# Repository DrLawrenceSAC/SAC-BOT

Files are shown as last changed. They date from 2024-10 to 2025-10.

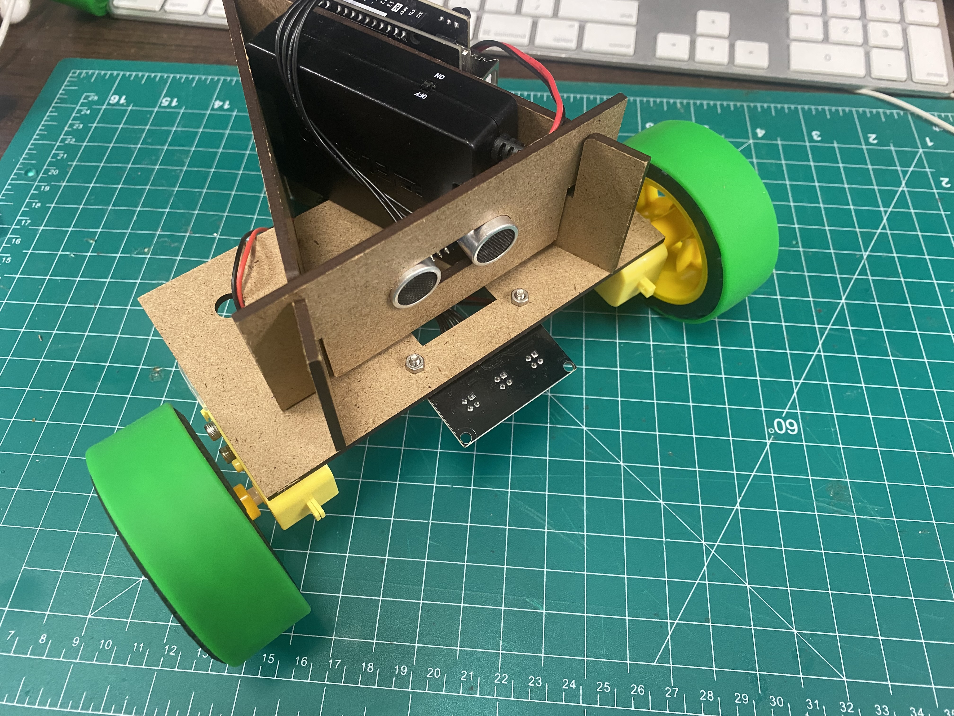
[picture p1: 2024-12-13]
RescueLine/images/IMG_2231.jpg

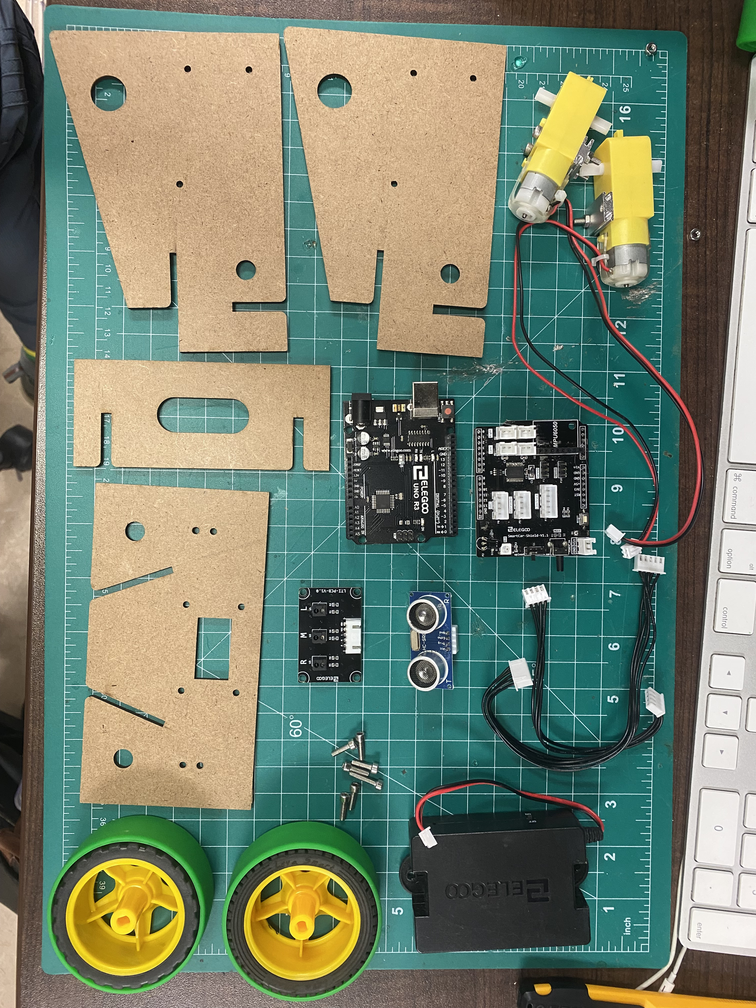
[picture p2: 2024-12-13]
RescueLine/images/IMG_2234.jpg

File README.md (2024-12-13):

# SAC-BOT
A repository for the design and development of low-cost, open-source, beginner robotics platforms tailored to competition in RoboCup Junior events.

The design goals for these designs are as follows:
- low-cost for ease of addoption within and beyond our program
- functional, not perfect - allowing immediate engagement, and encouraing student-led modification and improvement.
- designed for specific goals of [RoboCup Junior](https://www.robocup.org/)

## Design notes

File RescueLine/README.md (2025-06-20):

# Rescue - Line

A project to create a simple, functional, low-cost robot for use in RoboCup Junior Rescue Line competition. [Full competition information and rules can be found here](https://junior.robocup.org/rcj-rescue-line/).

The current design (version 7.4) is created to use as many simple parts that may be available in a given technology classroom (TT motors, arduino boards etc.)

The design files include laser cutting files and fusion 360 design files. The design is created to be cut from 3 mm (1/8 inch) thick MDF wood. It can be modified and improved, made out of cardboard or have components hot-glued on. The design is intentionally functional, but not optimal. This is a choice to encourage student design and modification in the spirit of RoboCup.

A video of the working robot showing line following and obstacle avoidance in a student activity is included in this directory.

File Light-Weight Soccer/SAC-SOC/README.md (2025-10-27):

# SAC-SOC

A minimal robot based on the simple design of the SAC-BOT for soccer robot construction.

## Stage One: Robotic Design Overview

### Plate 1 - Drive System

- **Motors:** Four TT motors positioned at 90° from each other
- **Wheels:** Standard plastic wheels (utilizing slipperiness for omni-drive functionality)
- **Assembly:** Motors bolted into place
- **Wiring:** Four wires run upward to Plate 2

### Plate 2 - Control System

- **Microcontroller:** Arduino Uno
- **Motor Control:** Motor controller mounted
- **Servos:** Two servos mounted for Plate 3 positioning

### Plate 3 - Sensor Array

- **Location:** Positioned above the motor driver
- **Sensors:** IR sensors with cicada pattern angle detection
- **Purpose:** Player ball detection

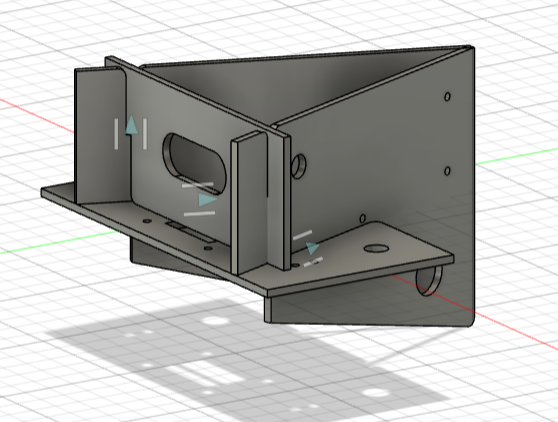
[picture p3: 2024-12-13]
RescueLine/images/2425-RoboCup-SACBOTV6.png

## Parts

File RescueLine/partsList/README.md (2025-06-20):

# Parts List

Below are the parts required for the SAC-BOT rescue line robot. A source link to supplier DigiKey is also included.

List is shared at (digikey.ca here)[https://www.digikey.ca/en/mylists/list/CZCZJ5AE1T].

The above link includes several extra parts (jumper wires, bolts and nuts) that might also be needed.

Not included! -> battery and battery holder we use a two-cell 18650 Lithium batter holder with a case. No sources from digikey, many on amazon and other providers.

| Digi-Key Part Number | Manufacturer | Manufacturer Part Number | Requested Part Number | Description | Customer Reference | Quantity | Unit Price | Extended Price |
| --- | --- | --- | --- | --- | --- | --- | --- | --- |
| 1738-1228-ND | DFRobot | DFR0216 | 1738-1228-ND | DFRDUINO UNO V3.0 ATMEGA328P | 1 | 19.17 | $19.17 | $19.17 |
| 1738-1078-ND | DFRobot | DRI0009 | 1738-1078-ND | 2A MOTOR SHIELD FOR ARDUINO | 1 | 20.66 | $20.66 | $20.66 |
| 1597-114090050-ND | Seeed Technology Co., Ltd | 1.14E+08 | 1597-114090050-ND | STANDARD MOTOR 210 RPM 3-7.2V | 2 | 1.9 | $3.80 | $3.80 |
| 1528-2711-ND | Adafruit Industries LLC | 3942 | 1528-2711-ND | ULTRASONIC SENSOR SONAR DISTANCE | 1 | 6.26 | $6.26 | $6.26 |
| 1568-1556-ND | SparkFun Electronics | SEN-11769 | 1568-1556-ND | SPARKFUN REDBOT SENSOR - LINE FO | 3 | 5.2 | $15.60 | $15.60 |
| 1528-2587-ND | Adafruit Industries LLC | 3763 | 1528-2587-ND | THIN WHITE WHEEL FOR TT DC GEARB | 2 | 2.38 | $4.76 | $4.76 |
| | | | | | | |Total: | $70.25 |

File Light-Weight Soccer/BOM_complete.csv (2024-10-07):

link | name | cost(cad) | amount | purpose
https://www.aliexpress.com/item/1005001456186625.html | WeAct BlackPill STM32F411CEU6 STM32F411 STM32F4 STM32 Core Board Learning Board Development Micropython | $5 | 2 | central processor
https://www.sparkfun.com/products/15335 | SparkFun 9DoF IMU Breakout - ICM-20948 (Qwiic) | $25.50 | 1 | IMU
N/A | IR PCB | $20 (Depending on bulk pricing) | 1 | IR Ball detection
N/A | Colour Sensor PCB | $40 | 1 | line detection
https://www.aliexpress.com/item/1005006213948214.html | JGA25-370 Mini Motor DC 12 Volt 3V 6V 24V High Torque Low Speed Reversed Electric Motor Reduction Engine 12v Gear Motor | $6 | 4 | Motors
N/A | Main PCB | $20 | 1 | Main PCB for mounting hardware
N/A | Misc Hardware/3D prints | $10 | 1 | Misc
https://www.amazon.ca/daier-2-5-4-Connector-200mm-Female/dp/B01DUC1S14 | daier 20 Sets Jst XH 2.54 4 Pin Connector Plug Male with 200mm Wire & Female Connector | $0.50 | 1 | Connector for IR PCB and connector joint
https://www.pololu.com/product/4733 | MP6550 Single Brushed DC Motor Driver Carrier | $6.31 | 4 | Motor Drivers
https://www.amazon.ca/Zeee-1300mAh-Quadcopter-Helicopter-Airplane/dp/B08CDT38CL | Zeee 11.1V 1300mAh Lipo Battery 120C 3S RC Battery with XT60 Plug for FPV Racing Drone Quadcopter Helicopter Airplane RC Boat RC Car RC Models(2 Pack) | $25 | 1 | Battery
https://www.pololu.com/product/2858 | Pololu 5V 2.5A Step-Down Voltage Regulator D24V22F5 | $16.58 | 1 | Regulator - Step Down
https://www.amazon.ca/2-54MM-Female-Single-Connector-Wires/dp/B07YJ2RKYF?s=industrial | 30 Sets JST XH 2.54MM 2 Pin Female Single Connector with Flat Wires 100MM 1007 26AWG | $0.50 | 1 | Motor to Board connector

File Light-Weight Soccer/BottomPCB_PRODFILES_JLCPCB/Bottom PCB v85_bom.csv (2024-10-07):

Comment | Designator | Footprint | LCSC Part #
1k | R1 R10 R11 R12 R13 R14 R15 R16 R17 | 0603
20 | R2 R3 R4 R5 R6 R7 R8 R9 | RESC3224X71
100nF | C1 C2 C3 C4 | WCAP-CSGP_0603_W
ICM-20948_SPARKFUN_I2C | U$2 | ICM-20948_SPARKFUN_I2C
JE2835ARD-N-0001A0000-N0000001 | LED1 LED2 LED3 LED4 LED5 LED6 LED7 LED8 | JE2835ARDN0001A0000N0000001
LED_GREEN | D1 | LEDC1005X25N_FLAT-G
MINISTM32F4X1 | U$1 | MINISTM32F4X1
MP6550_POLOLU | M1 M2 M3 M4 | MP6550_POLOLU
PINHD-1X2 | JP3 JP4 JP5 JP6 | 1X02
PINHD-1X4/90 | JP1 | 1X04/90
PINHD-1X55X2MM | JP2 JP7 JP8 JP9 | 1_05X2MM
SRD-12VDC-SL-C | K1 | RELAY_SRD-12VDC-SL-C
SSSF021500 | S1 S2 | SSSF021500
VBPW34S | D2 D3 D4 D5 D6 D7 D8 D9 | VBPW34S
XT60-M | J1 | AMASS_XT60-M

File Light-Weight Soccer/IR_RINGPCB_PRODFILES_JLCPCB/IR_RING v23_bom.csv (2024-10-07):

Comment | Designator | Footprint | LCSC Part #
MINISTM32F4X1 | U$1 | MINISTM32F4X1
PINHD-1X4 | JP1 | 1X04
PINHD-1X4/90 | JP2 JP3 JP4 JP5 JP6 | 1X04/90
TSSP4038 | IC1 IC2 IC3 IC4 IC5 IC6 IC7 IC8 IC9 IC10 IC11 IC12 | TSSP4038

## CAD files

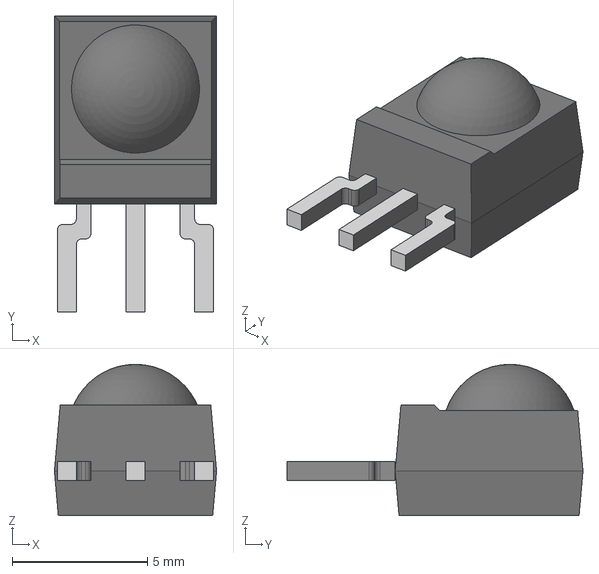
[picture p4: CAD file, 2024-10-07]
Light-Weight Soccer/Design Files/3D Models/TSSP4038_v1.step
6.00 x 10.9 x 5.60 mm

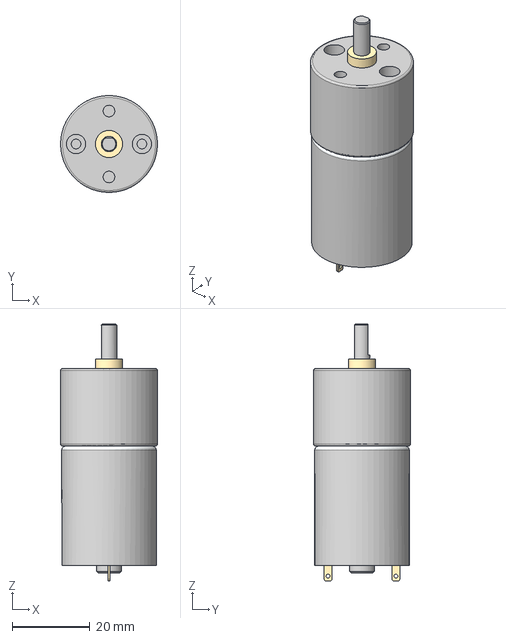
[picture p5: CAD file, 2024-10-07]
Light-Weight Soccer/Design Files/3D Models/dc motor2 v1_v1.step
25.0 x 25.0 x 66.3 mm

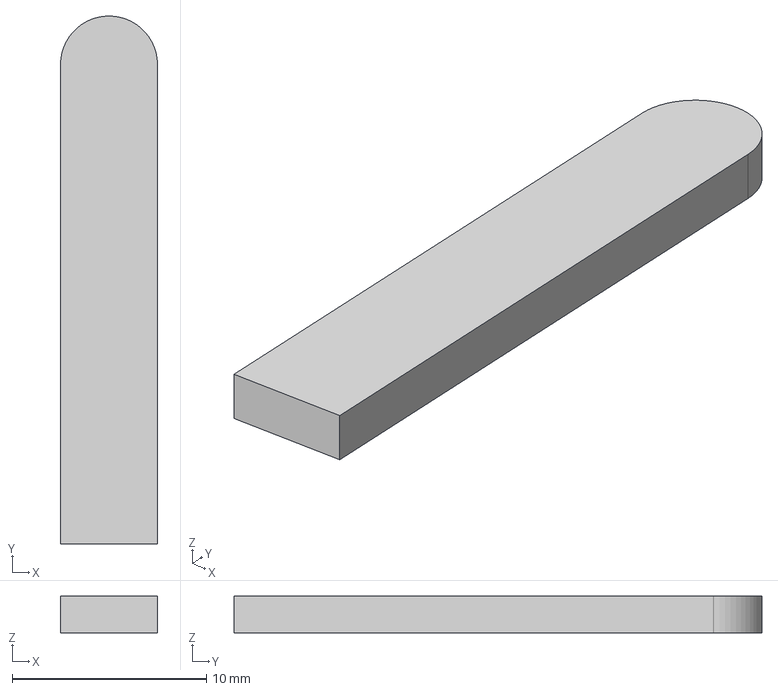
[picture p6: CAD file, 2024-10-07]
Light-Weight Soccer/Design Files/3D Models/Open Funnel_Component2_v1.step
5.00 x 27.2 x 1.90 mm

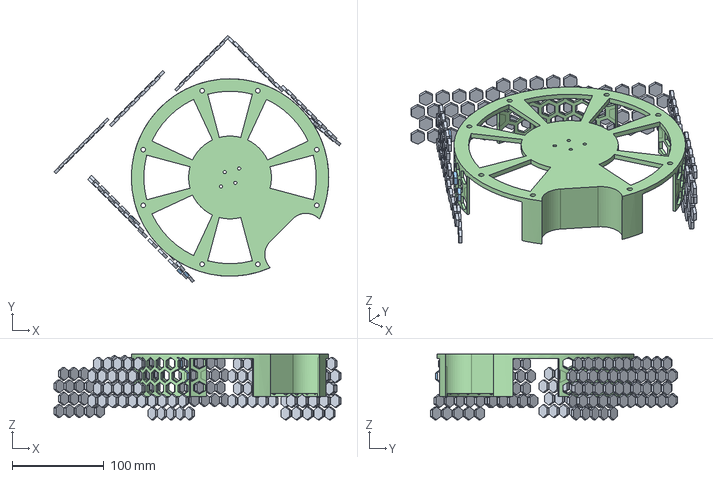
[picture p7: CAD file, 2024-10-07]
Light-Weight Soccer/Design Files/3D Models/Base Cover_v4.step
312.5 x 269.0 x 71.3 mm
honeycomb design x 7
honeycomb design v0(Mirror) x 3

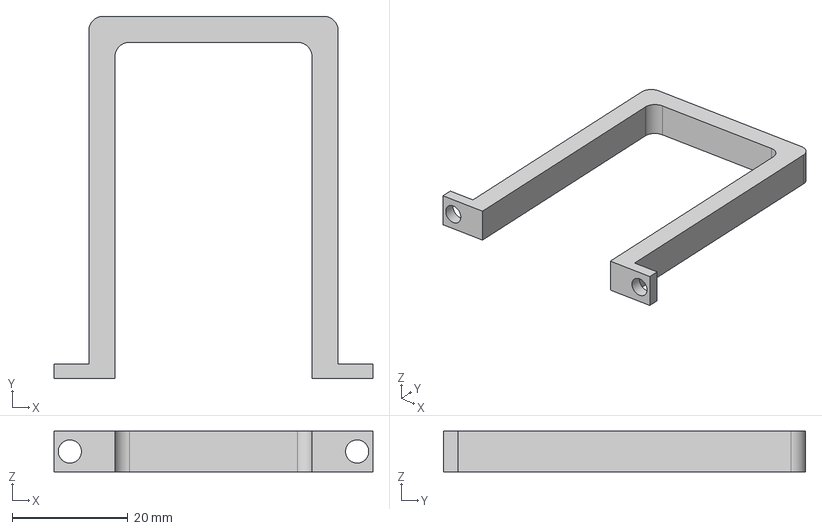
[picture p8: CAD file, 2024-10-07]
Light-Weight Soccer/Design Files/3D Models/Handle_v3.step
55.0 x 62.5 x 7.00 mm

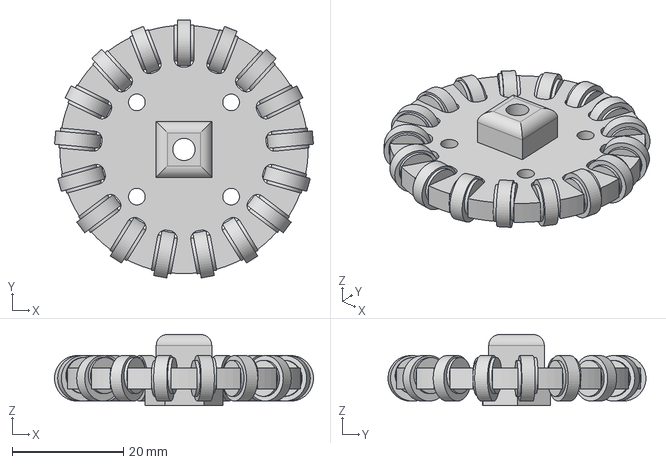
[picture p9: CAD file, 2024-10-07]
Light-Weight Soccer/Design Files/3D Models/gtf_robots_50mm_x_6mm_nGoLKr v4_v1.step
46.6 x 46.4 x 12.8 mm

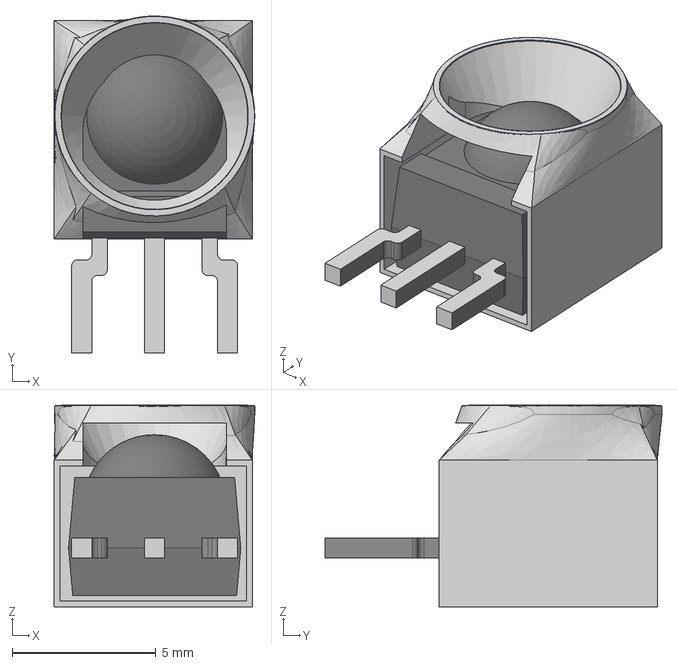
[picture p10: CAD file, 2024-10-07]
Light-Weight Soccer/Design Files/3D Models/Closed Funnel_v1.step
6.99 x 11.7 x 7.03 mm
Open Funnel v1
TSSP4038

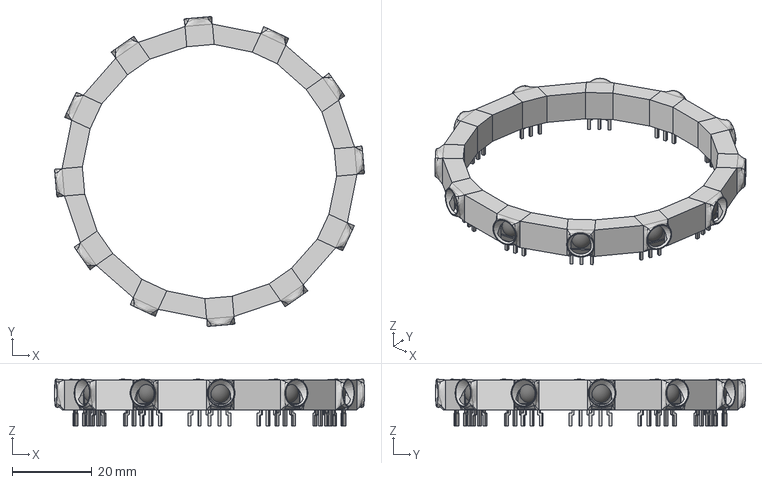
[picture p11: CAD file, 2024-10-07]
Light-Weight Soccer/Design Files/3D Models/IR_RING_MODEL_v2.step
77.8 x 77.8 x 11.7 mm
Open Funnel v1 x 12
TSSP4038 x 12

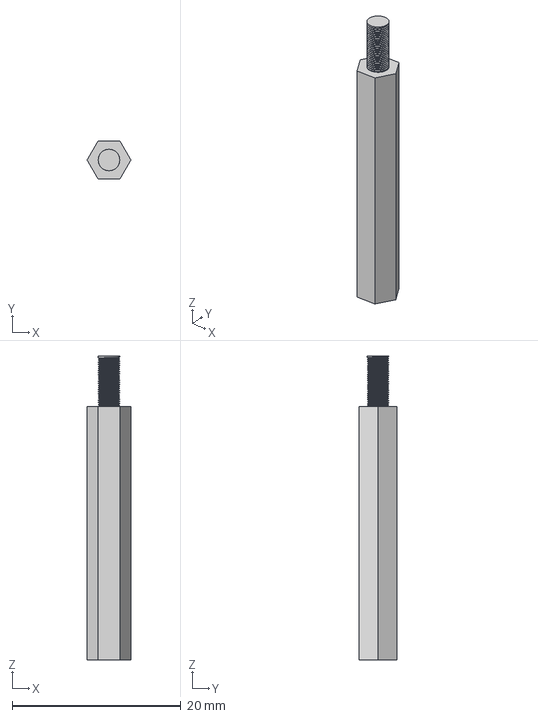
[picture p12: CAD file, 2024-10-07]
Light-Weight Soccer/Design Files/3D Models/stand off v1_v1.step
5.20 x 4.50 x 36.0 mm

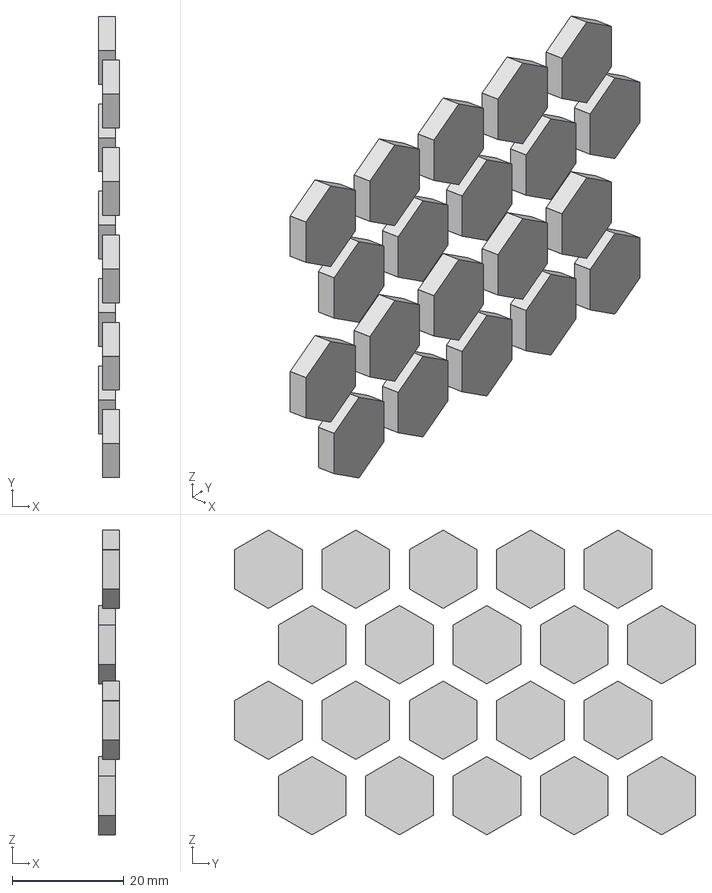
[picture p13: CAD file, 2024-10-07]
Light-Weight Soccer/Design Files/3D Models/honeycomb design_v1.step
3.72 x 82.4 x 54.5 mm

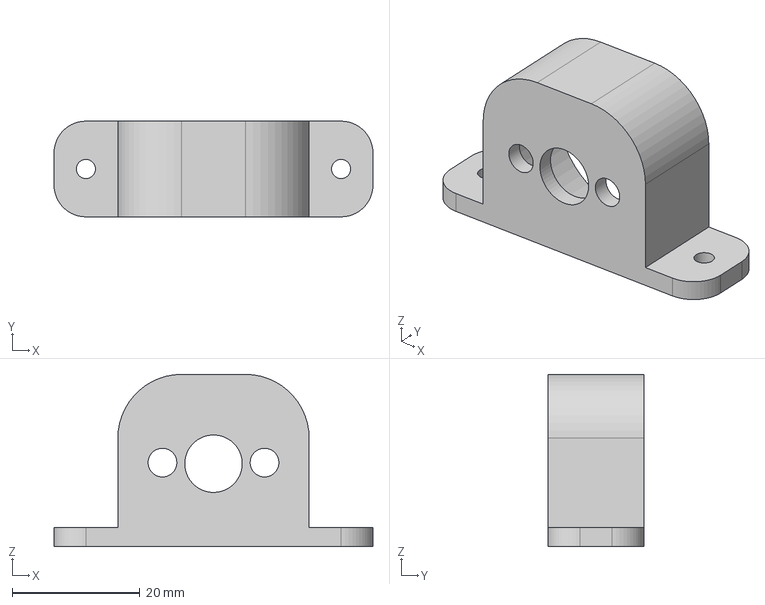
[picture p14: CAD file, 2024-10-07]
Light-Weight Soccer/Design Files/3D Models/motor mount v5_v2.step
50.0 x 15.0 x 27.0 mm

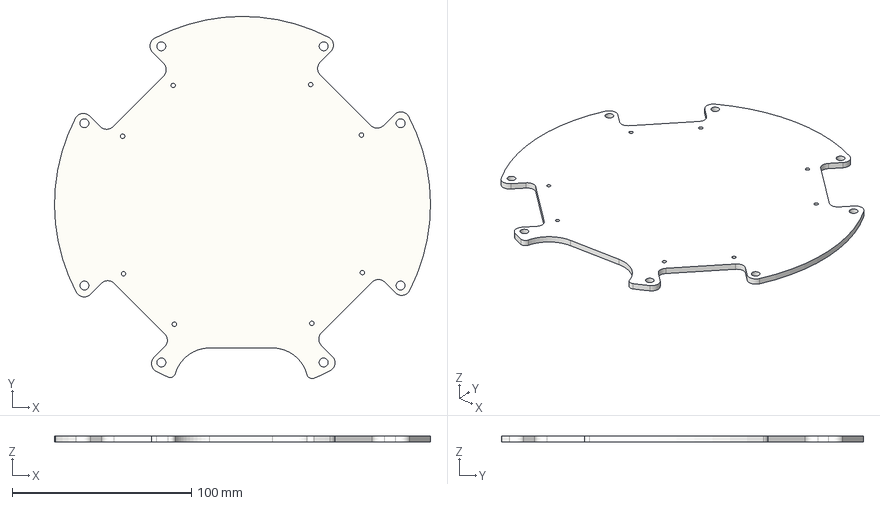
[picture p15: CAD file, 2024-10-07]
Light-Weight Soccer/Design Files/3D Models/Bottom Shape v16_v1.step
210.0 x 202.3 x 3.50 mm

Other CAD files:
Light-Weight Soccer/Design Files/3D Models/Assembly_v13.f3d
Light-Weight Soccer/Design Files/3D Models/Bottom Shape v16_v1.f3d
Light-Weight Soccer/Design Files/3D Models/Closed Funnel_v1.f3d
Light-Weight Soccer/Design Files/3D Models/Handle_v3.f3d
Light-Weight Soccer/Design Files/3D Models/IR_RING_MODEL_v2.f3d
Light-Weight Soccer/Design Files/3D Models/Open Funnel_Component2_v1.f3d
Light-Weight Soccer/Design Files/3D Models/TSSP4038_v1.f3d
Light-Weight Soccer/Design Files/3D Models/dc motor2 v1_v1.f3d
Light-Weight Soccer/Design Files/3D Models/gtf_robots_50mm_x_6mm_nGoLKr v4_v1.f3d
Light-Weight Soccer/Design Files/3D Models/honeycomb design_v1.f3d
Light-Weight Soccer/Design Files/3D Models/motor mount v5_v2.f3d
Light-Weight Soccer/Design Files/3D Models/stand off v1_v1.f3d
Light-Weight Soccer/Design Files/ICM-20948/SparkFun_IMU_Breakout_ICM-20948 v3.f3z
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

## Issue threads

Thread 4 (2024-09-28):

SAC-BOT/Light-Weight Soccer/BottomPCB_PRODFILES_JLCPCB: Fix the properties for the BOM and the CPL in Fusion 360

TheSoupMasta, 2024-09-28:
Need to fix the BOM and CPL files to point to the right components inside of JLCPCB, since some were replaced inside the part picker menu of JLCPCB.

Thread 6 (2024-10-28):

SAC-BOT/Light-Weight Soccer: Fix library issues that resulted from wrong pad default size for most custom footprints.

TheSoupMasta, 2024-10-28:
Library issues caused by the library issues. Pad sizes defaulted to 0.5mm pin width when most standoff pins are about 1mm. Need to fix and change pad sizes and reroute the new updated libraries.

TheSoupMasta, 2024-10-28:
Fixed for top PCB, waiting on bottom.

TheSoupMasta, 2024-11-09:
Fixed

TheSoupMasta, 2024-11-09:
Will pull request with other changes, fixed locally for now

Closed 2024-11-09.

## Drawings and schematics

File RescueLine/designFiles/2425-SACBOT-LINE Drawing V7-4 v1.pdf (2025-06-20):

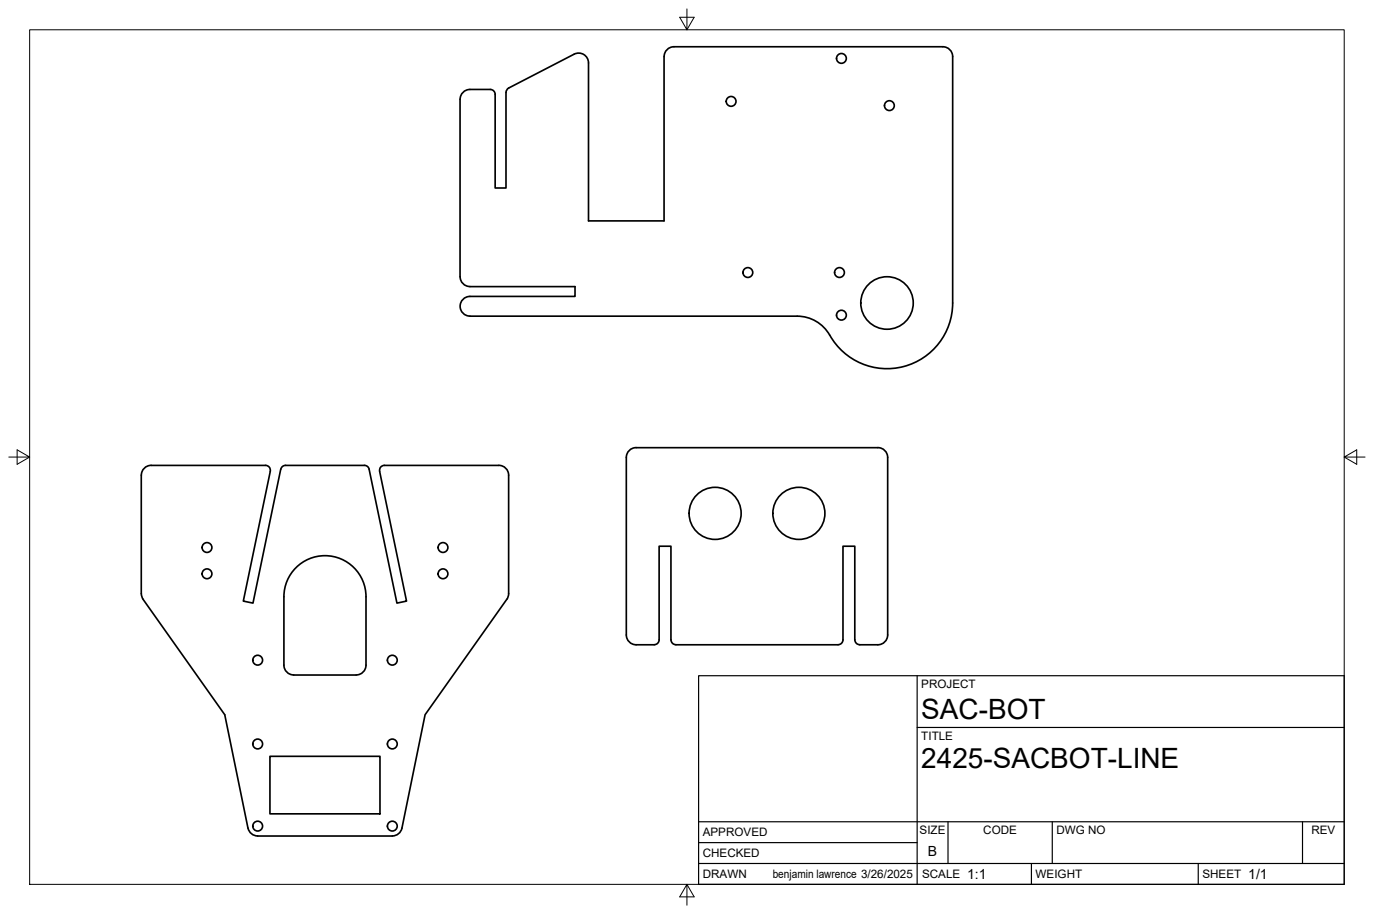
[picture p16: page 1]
SIZE; CODE; DWG NO; REV; benjamin lawrence 3/26/2025

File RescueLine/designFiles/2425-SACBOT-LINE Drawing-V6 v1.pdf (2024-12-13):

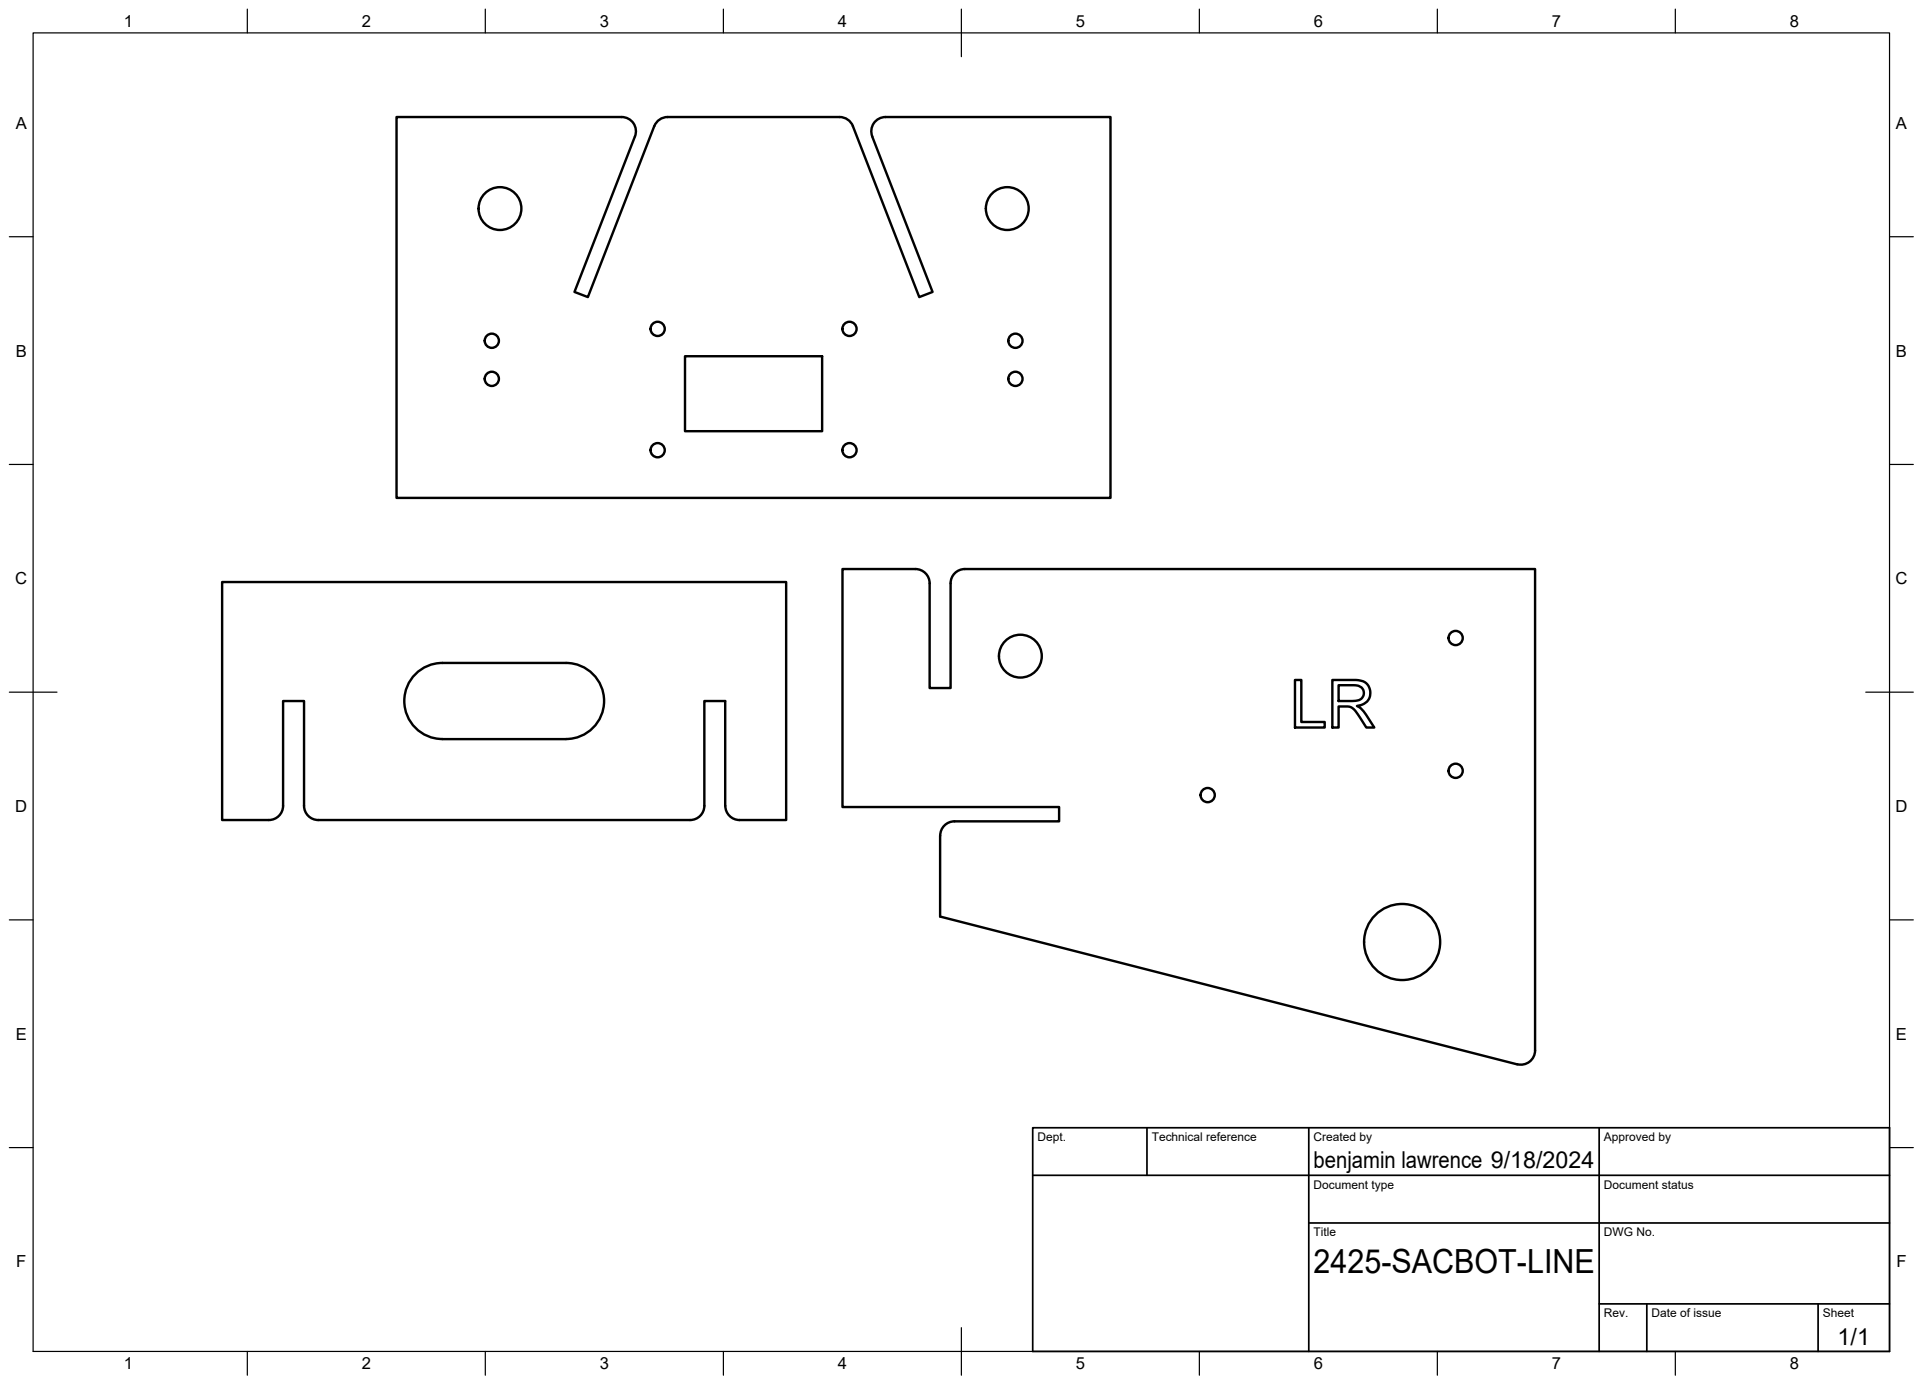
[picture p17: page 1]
Title; DWG No.; Rev.; Date of issue; Sheet

Dept. | Technical reference | Created by benjamin lawrence 9/18/2024 | Approved by

Document type | Document status

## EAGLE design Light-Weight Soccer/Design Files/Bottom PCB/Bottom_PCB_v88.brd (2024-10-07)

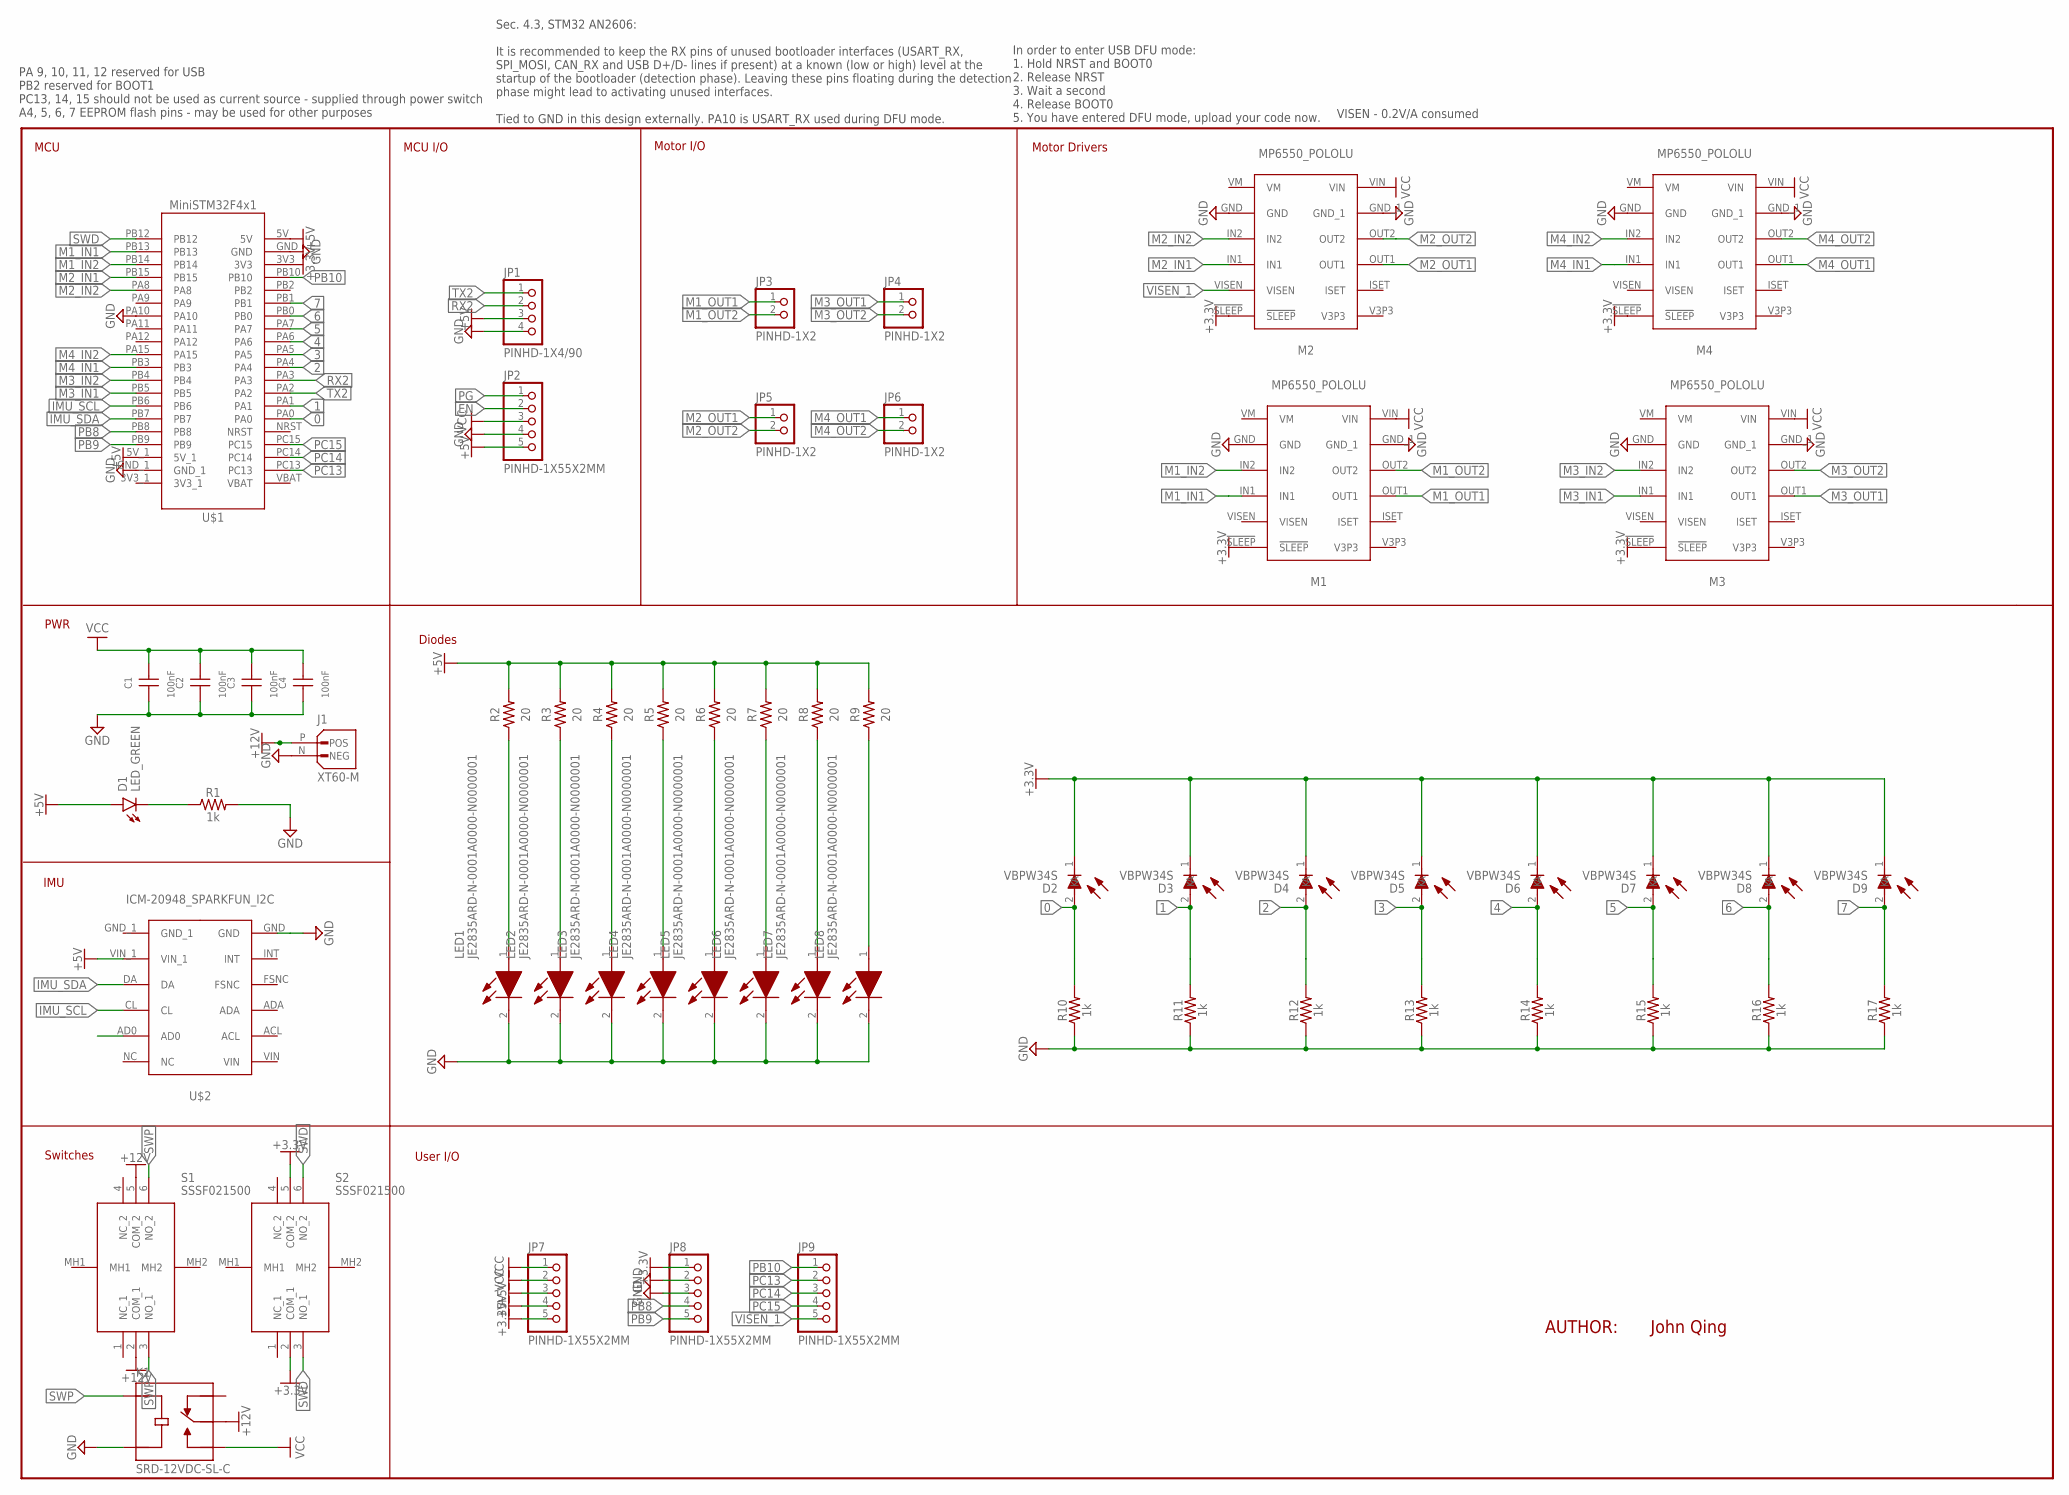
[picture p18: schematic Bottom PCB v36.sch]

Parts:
C1, C2, C3, C4: 100nF; WCAP-CSGP_0603_W
D1: LED_GREEN; LEDC1005X25N_FLAT-G
D2, D3, D4, D5, D6, D7, D8, D9: VBPW34S
J1: XT60-M; AMASS_XT60-M
JP1: PINHD-1X4/90; 1X04/90
JP2, JP7, JP8, JP9: PINHD-1X55X2MM; 1_05X2MM
JP3, JP4, JP5, JP6: PINHD-1X2; 1X02
K1: SRD-12VDC-SL-C; RELAY_SRD-12VDC-SL-C
LED1, LED2, LED3, LED4, LED5, LED6, LED7, LED8: JE2835ARD-N-0001A0000-N0000001; JE2835ARDN0001A0000N0000001
M1, M2, M3, M4: MP6550_POLOLU
R1, R10, R11, R12, R13, R14, R15, R16, R17: 1k; 0603
R2, R3, R4, R5, R6, R7, R8, R9: 20; RESC3224X71
S1, S2: SSSF021500
U$1: MINISTM32F4X1
U$2: ICM-20948_SPARKFUN_I2C

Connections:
0: D2.2 (A), R10.2, U$1.PA0
1: D3.2 (A), R11.2, U$1.PA1
2: D4.2 (A), R12.2, U$1.PA4
3: D5.2 (A), R13.2, U$1.PA5
4: D6.2 (A), R14.2, U$1.PA6
5: D7.2 (A), R15.2, U$1.PA7
6: D8.2 (A), R16.2, U$1.PB0
7: D9.2 (A), R17.2, U$1.PB1
+3.3V: D2.1 (K), D3.1 (K), D4.1 (K), D5.1 (K), D6.1 (K), D7.1 (K), D8.1 (K), D9.1 (K), JP7.5, JP8.1, M1.!SLEEP, M2.!SLEEP, M3.!SLEEP, M4.!SLEEP, S2.2 (COM_1), S2.5 (COM_2), U$1.3V3
+5V: D1.A, JP1.3, JP2.5, JP7.3, JP7.4, R2.2, R3.2, R4.2, R5.2, R6.2, R7.2, R8.2, R9.2, U$1.5V, U$1.5V_1, U$2.VIN_1
+12V: J1.P (POS), K1.COM, S1.2 (COM_1), S1.5 (COM_2)
EN: JP2.2
GND: C1.1, C2.1, C3.1, C4.1, J1.N (NEG), JP1.4, JP2.4, JP8.2, JP8.3, K1.COIL2, LED1.2 (K), LED2.2 (K), LED3.2 (K), LED4.2 (K), LED5.2 (K), LED6.2 (K), LED7.2 (K), LED8.2 (K), M1.GND, M1.GND_1, M2.GND, M2.GND_1, M3.GND, M3.GND_1, M4.GND, M4.GND_1, R1.2, R10.1, R11.1, R12.1, R13.1, R14.1, R15.1, R16.1, R17.1, U$1.GND, U$1.GND_1, U$1.PA10, U$2.GND
IMU_SCL: U$1.PB6, U$2.CL
IMU_SDA: U$1.PB7, U$2.DA
M1_IN1: M1.IN1, U$1.PB13
M1_IN2: M1.IN2, U$1.PB14
M1_OUT1: JP3.1, M1.OUT1
M1_OUT2: JP3.2, M1.OUT2
M2_IN1: M2.IN1, U$1.PB15
M2_IN2: M2.IN2, U$1.PA8
M2_OUT1: JP5.1, M2.OUT1
M2_OUT2: JP5.2, M2.OUT2
M3_IN1: M3.IN1, U$1.PB5
M3_IN2: M3.IN2, U$1.PB4
M3_OUT1: JP4.1, M3.OUT1
M3_OUT2: JP4.2, M3.OUT2
M4_IN1: M4.IN1, U$1.PB3
M4_IN2: M4.IN2, U$1.PA15
M4_OUT1: JP6.1, M4.OUT1
M4_OUT2: JP6.2, M4.OUT2
unnamed: D1.C, R1.1
unnamed: LED1.1 (A), R2.1
unnamed: LED2.1 (A), R3.1
unnamed: LED3.1 (A), R4.1
unnamed: LED4.1 (A), R5.1
unnamed: LED5.1 (A), R6.1
unnamed: LED6.1 (A), R7.1
unnamed: LED7.1 (A), R8.1
unnamed: LED8.1 (A), R9.1
PB8: JP8.4, U$1.PB8
PB9: JP8.5, U$1.PB9
PB10: JP9.1, U$1.PB10
PC13: JP9.2, U$1.PC13
PC14: JP9.3, U$1.PC14
PC15: JP9.4, U$1.PC15
PG: JP2.1
RX2: JP1.2, U$1.PA3
SWD: S2.3 (NO_1), S2.6 (NO_2), U$1.PB12
SWP: K1.COIL1, S1.3 (NO_1), S1.6 (NO_2)
TX2: JP1.1, U$1.PA2
VCC: C1.2, C2.2, C3.2, C4.2, JP2.3, JP7.1, JP7.2, K1.NO, M1.VIN, M2.VIN, M3.VIN, M4.VIN
VISEN_1: JP9.5, M2.VISEN

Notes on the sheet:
MCU
MCU I/O
Motor I/O
Motor Drivers
PWR
AUTHOR:
John Qing
IMU
Diodes
Switches
User I/O
PA 9, 10, 11, 12 reserved for USB PB2 reserved for BOOT1 PC13, 14, 15 should not be used as current source - supplied through power switch A4, 5, 6, 7 EEPROM flash pins - may be used for other purposes
Sec. 4.3, STM32 AN2606: It is recommended to keep the RX pins of unused bootloader interfaces (USART_RX, SPI_MOSI, CAN_RX and USB D+/D- lines if present) at a known (low or high) level at the startup of the bootloader (detection phase). Leaving these pins floating during the detection phase might l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
In order to enter USB DFU mode: 1. Hold NRST and BOOT0 2. Release NRST 3. Wait a second 4. Release BOOT0 5. You have entered DFU mode, upload your code now.
VISEN - 0.2V/A consumed

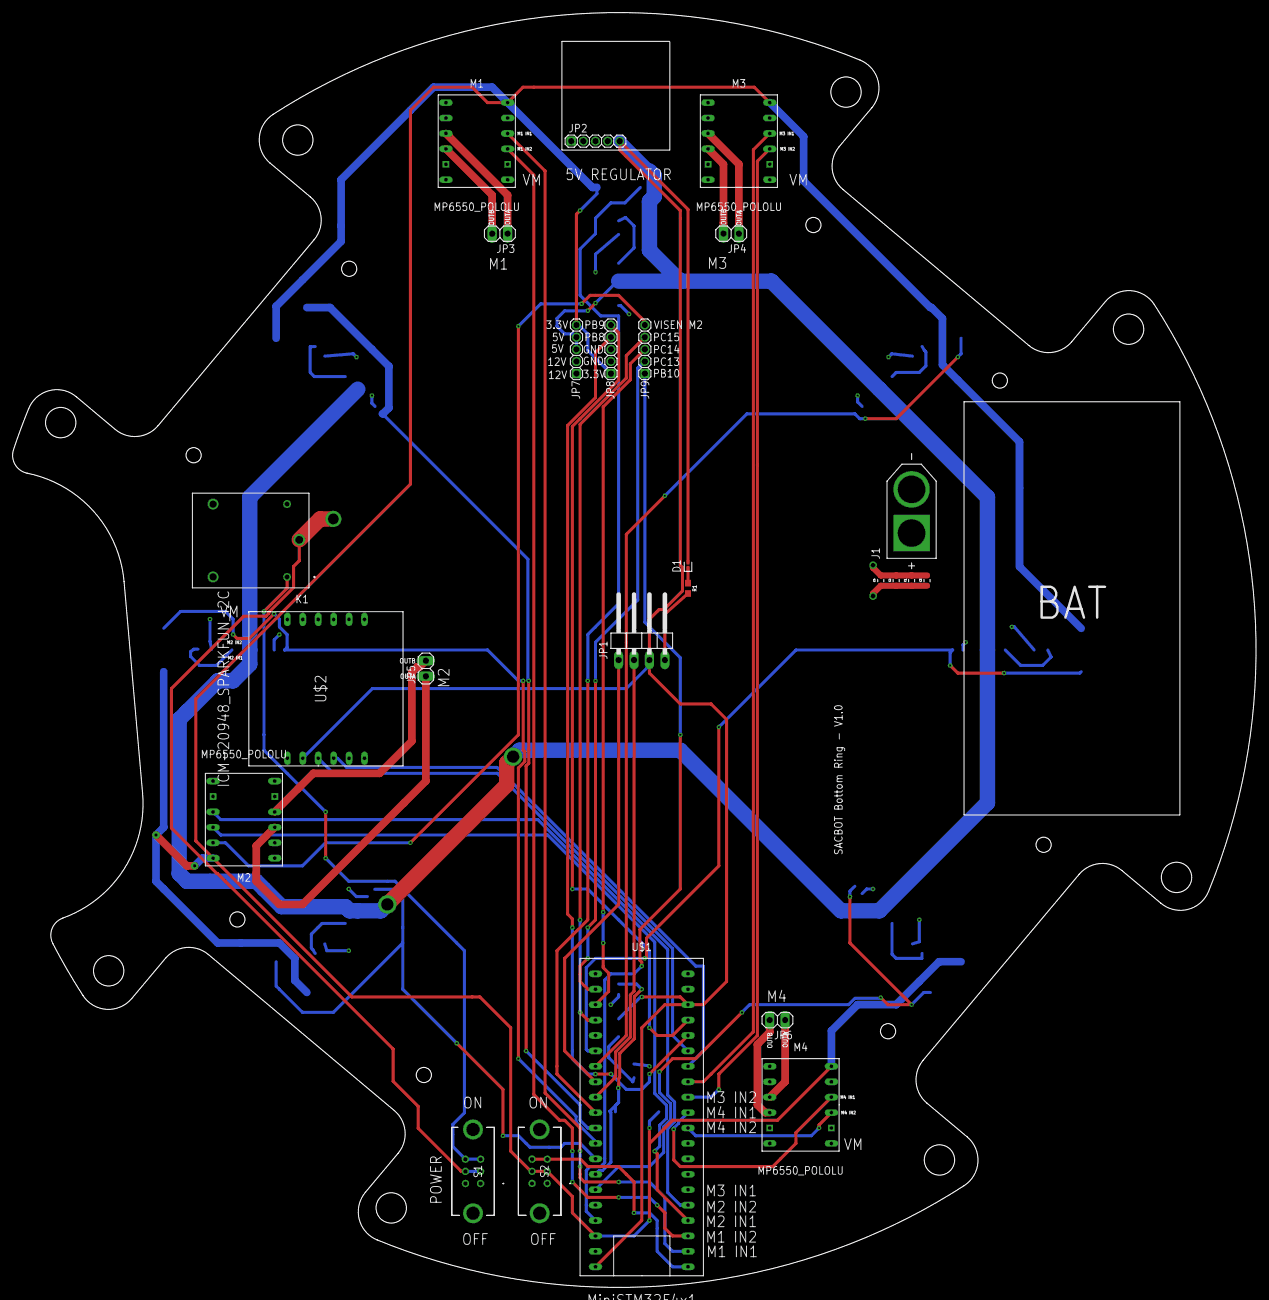
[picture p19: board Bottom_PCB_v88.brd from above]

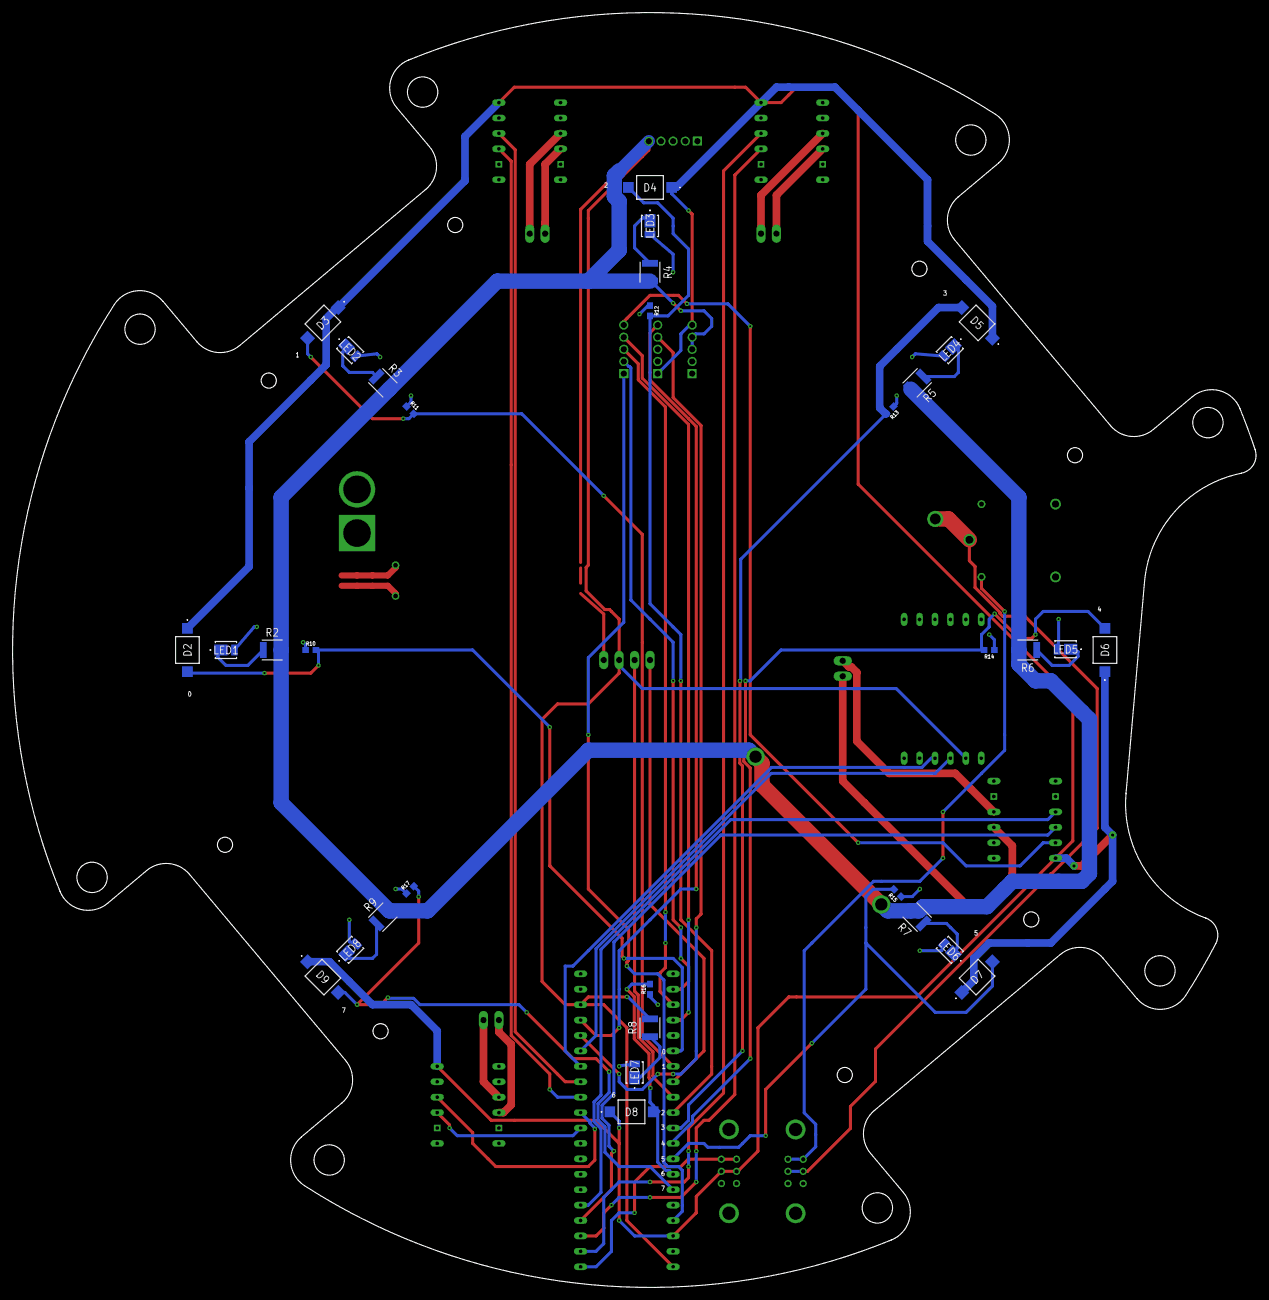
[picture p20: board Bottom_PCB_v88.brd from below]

Board: 4 copper layers, 204.8 x 210.0 mm, 57 parts (32 on the bottom side), 51 nets.

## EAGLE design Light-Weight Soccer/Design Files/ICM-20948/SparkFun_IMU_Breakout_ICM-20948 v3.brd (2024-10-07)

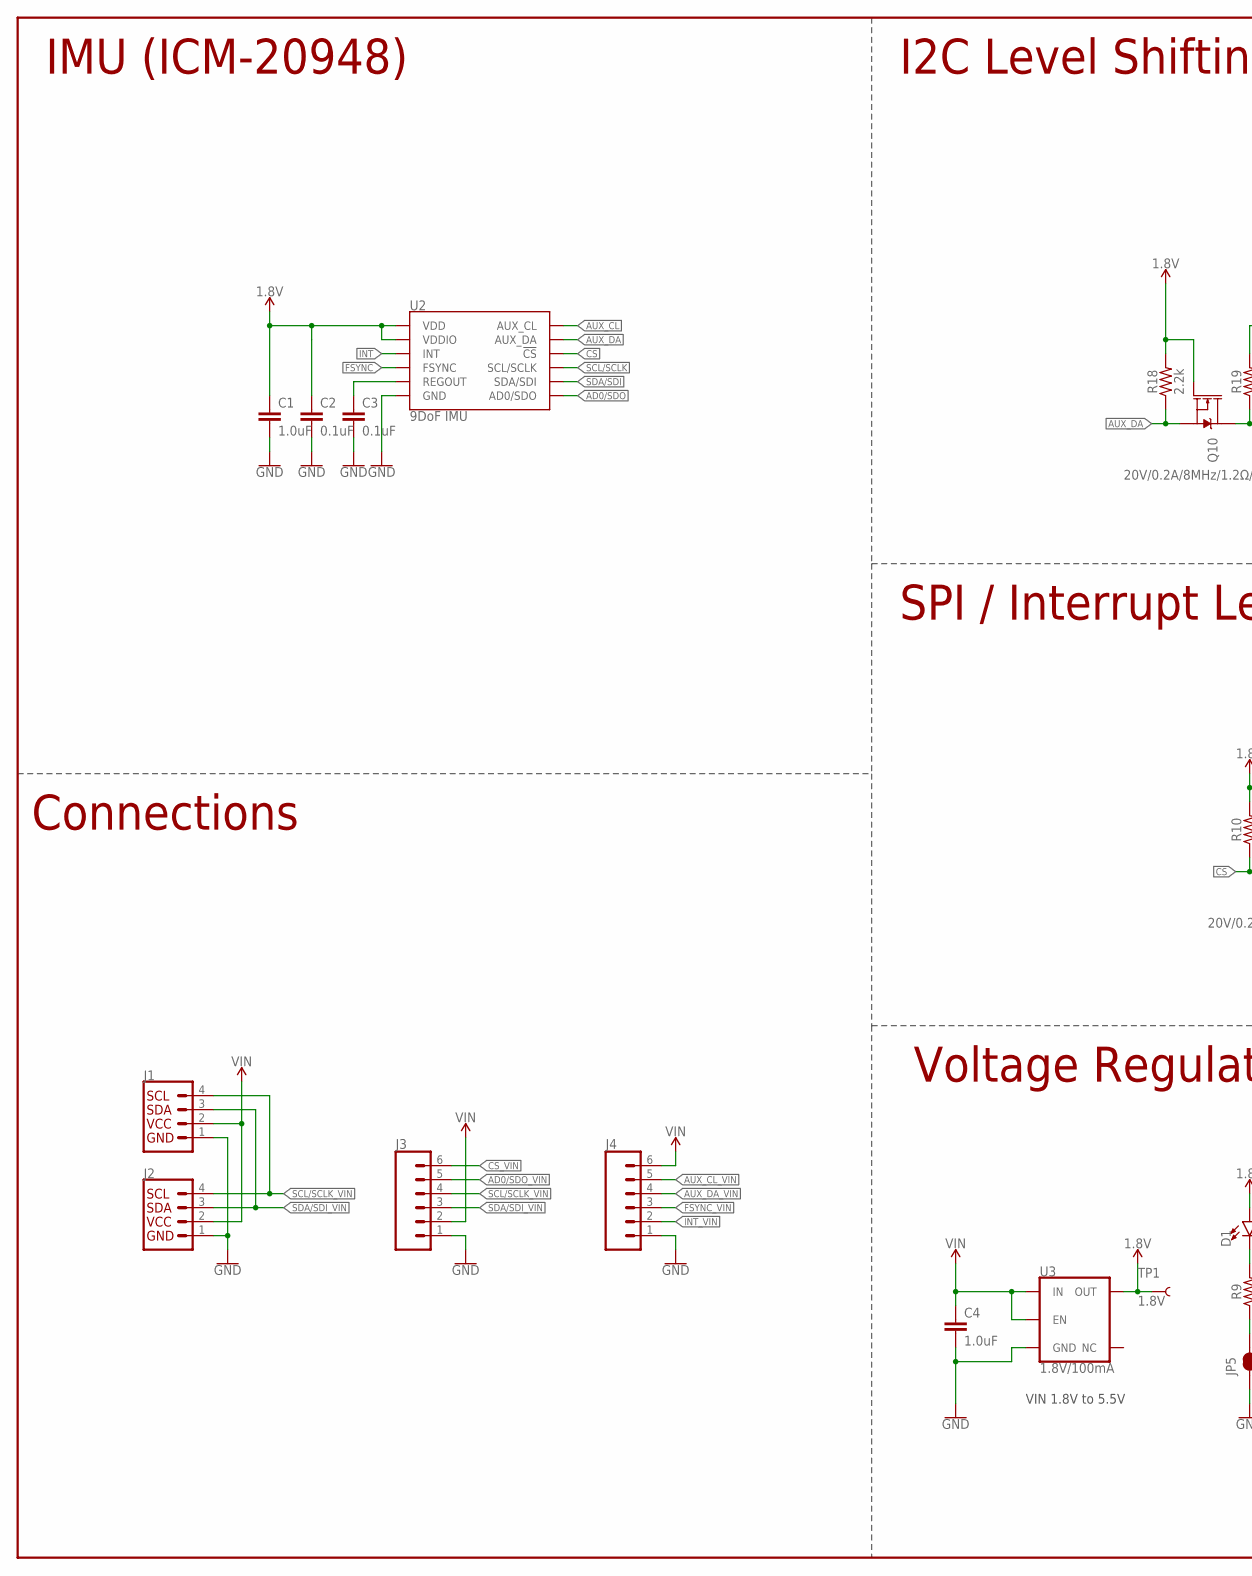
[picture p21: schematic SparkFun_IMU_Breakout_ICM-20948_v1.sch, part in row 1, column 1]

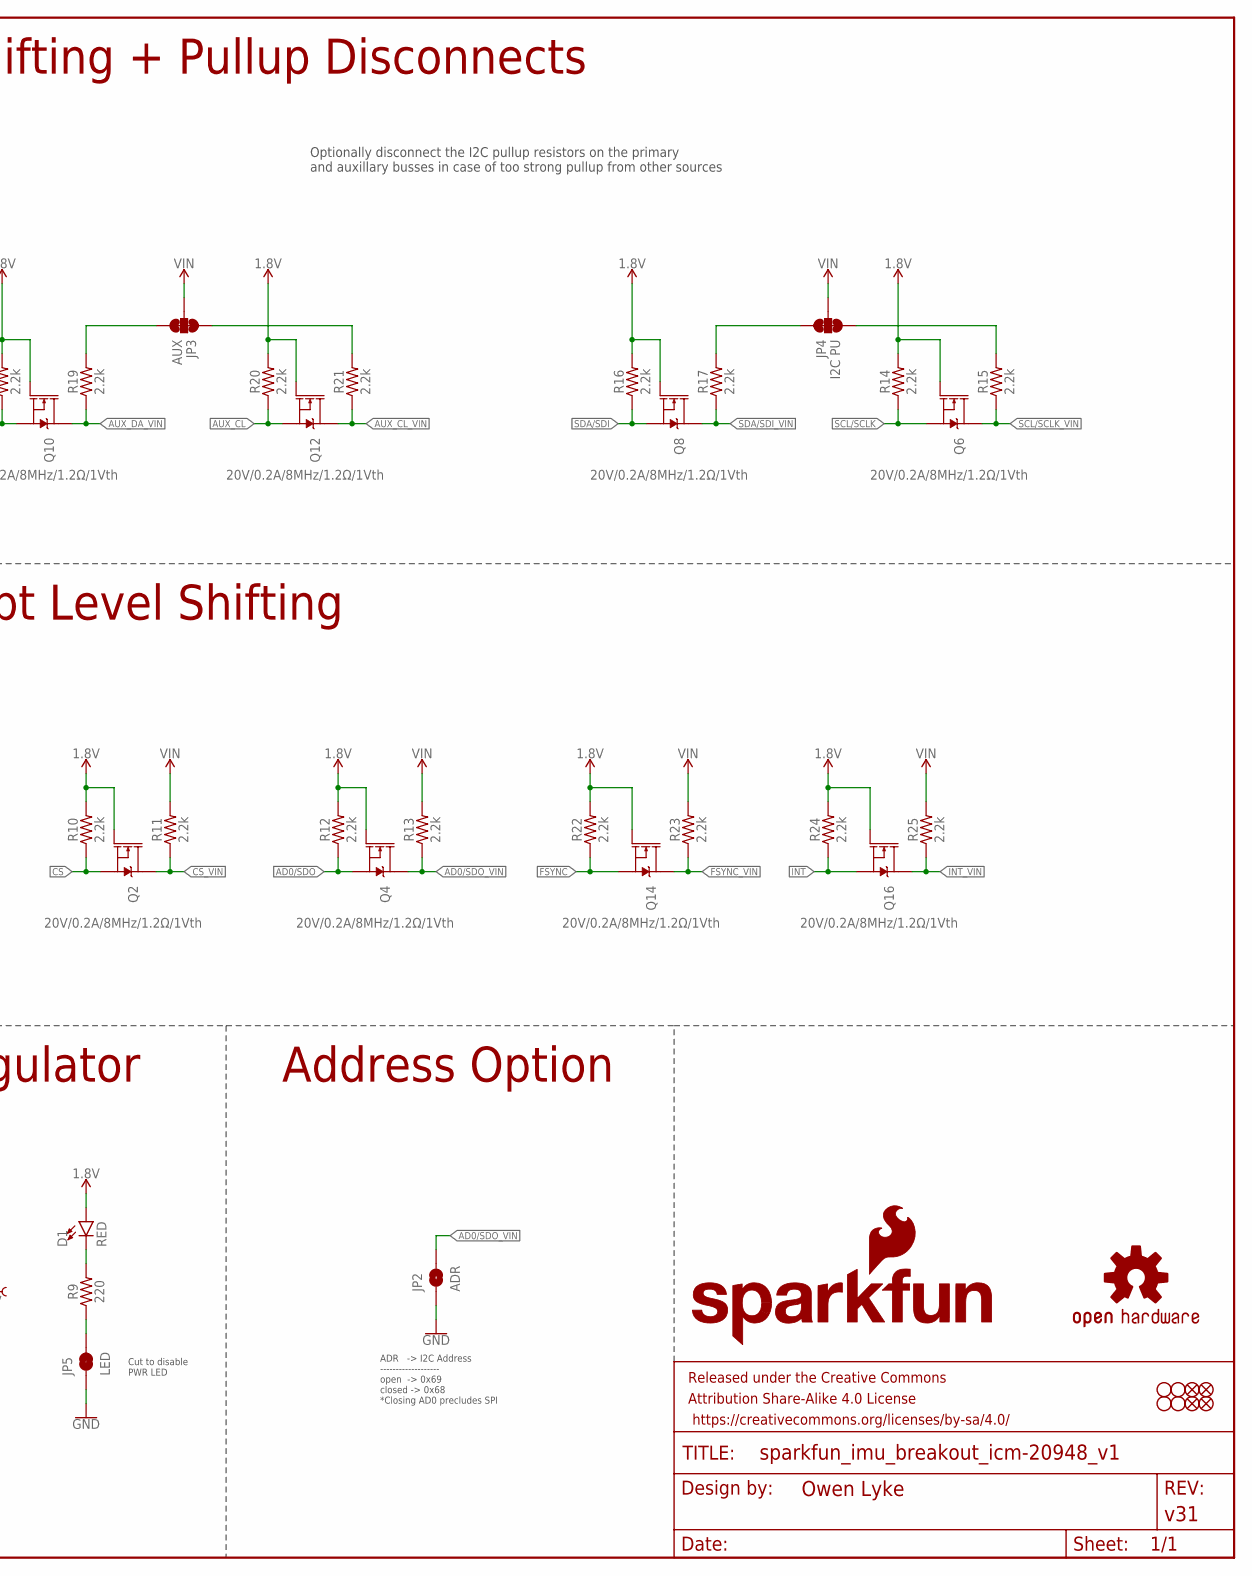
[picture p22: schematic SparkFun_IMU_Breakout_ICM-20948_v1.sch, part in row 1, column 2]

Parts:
C1, C4: 1.0uF; 0603
C2, C3: 0.1uF; 0603
D1: RED; LED-0603
FD1, FD2, FD3, FD4: FIDUCIAL1X2; FIDUCIAL-1X2
FRAME2: FRAME-LEDGER; CREATIVE_COMMONS
H1, H2, H3, H4: STAND-OFF
J1, J2: QWIIC_CONNECTORJS-1MM; JST04_1MM_RA
J3, J4: CONN_06NO_SILK_NO_POP; 1X06_NO_SILK
JP2: ADR; SMT-JUMPER_2_NO_SILK
JP3: AUX; SMT-JUMPER_3_2-NC_TRACE_SILK
JP4: I2C PU; SMT-JUMPER_3_2-NC_TRACE_SILK
JP5: LED; SMT-JUMPER_2_NC_TRACE_SILK
LOGO1: SFE_LOGO_NAME_FLAME.1_INCH; SFE_LOGO_NAME_FLAME_.1
LOGO2: OSHW-LOGOMINI; OSHW-LOGO-MINI
Q2, Q4, Q6, Q8, Q10, Q12, Q14, Q16: 20V/0.2A/8MHz/1.2Ω/1Vth; SOT-416FL
R9: 220; 0603
R10, R11, R12, R13, R14, R15, R16, R17, R18, R19, R20, R21, R22, R23, R24, R25: 2.2k; 0402-TIGHT
TP1: 1.8V; PAD.03X.03
U2: 9DoF IMU; QFN24-3X3
U3: 1.8V/100mA; SC70

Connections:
1.8V: C1.1, C2.1, D1.A, Q2.1 (G), Q4.1 (G), Q6.1 (G), Q8.1 (G), Q10.1 (G), Q12.1 (G), Q14.1 (G), Q16.1 (G), R10.2, R12.2, R14.2, R16.2, R18.2, R20.2, R22.2, R24.2, TP1.P$1, U2.8 (VDDIO), U2.13 (VDD), U3.5 (OUT)
!CS: Q2.2 (S), R10.1, U2.22 (!CS)
!CS!_VIN: J3.6, Q2.3 (D), R11.1
AD0/SDO: Q4.2 (S), R12.1, U2.9 (AD0/SDO)
AD0/SDO_VIN: J3.5, JP2.2, Q4.3 (D), R13.1
AUX_CL: Q12.2 (S), R20.1, U2.7 (AUX_CL)
AUX_CL_VIN: J4.5, Q12.3 (D), R21.1
AUX_DA: Q10.2 (S), R18.1, U2.21 (AUX_DA)
AUX_DA_VIN: J4.4, Q10.3 (D), R19.1
FSYNC: Q14.2 (S), R22.1, U2.11 (FSYNC)
FSYNC_VIN: J4.3, Q14.3 (D), R23.1
GND: C1.2, C2.2, C3.2, C4.2, J1.1, J2.1, J3.1, J4.1, JP2.1, JP5.1, U2.18 (GND), U2.20 (GND), U3.2 (GND)
INT: Q16.2 (S), R24.1, U2.12 (INT)
INT_VIN: J4.2, Q16.3 (D), R25.1
unnamed: C3.1, U2.10 (REGOUT)
unnamed: JP4.3, R15.2
unnamed: JP4.1, R17.2
unnamed: JP3.1, R21.2
unnamed: JP3.3, R19.2
unnamed: D1.C, R9.2
unnamed: JP5.2, R9.1
SCL/SCLK: Q6.2 (S), R14.1, U2.23 (SCL/SCLK)
SCL/SCLK_VIN: J1.4, J2.4, J3.4, Q6.3 (D), R15.1
SDA/SDI: Q8.2 (S), R16.1, U2.24 (SDA/SDI)
SDA/SDI_VIN: J1.3, J2.3, J3.3, Q8.3 (D), R17.1
VIN: C4.1, J1.2, J2.2, J3.2, J4.6, JP3.2, JP4.2, R11.2, R13.2, R23.2, R25.2, U3.1 (IN), U3.3 (EN)

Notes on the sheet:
VIN 1.8V to 5.5V
IMU (ICM-20948)
I2C Level Shifting + Pullup Disconnects
Connections
Voltage Regulator
SPI / Interrupt Level Shifting
ADR -> I2C Address ------------------- open -> 0x69 closed -> 0x68 *Closing AD0 precludes SPI
Optionally disconnect the I2C pullup resistors on the primary and auxillary busses in case of too strong pullup from other sources
Cut to disable PWR LED
Address Option

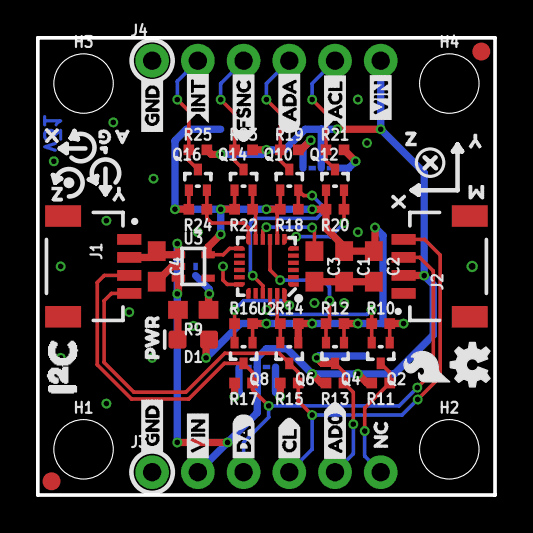
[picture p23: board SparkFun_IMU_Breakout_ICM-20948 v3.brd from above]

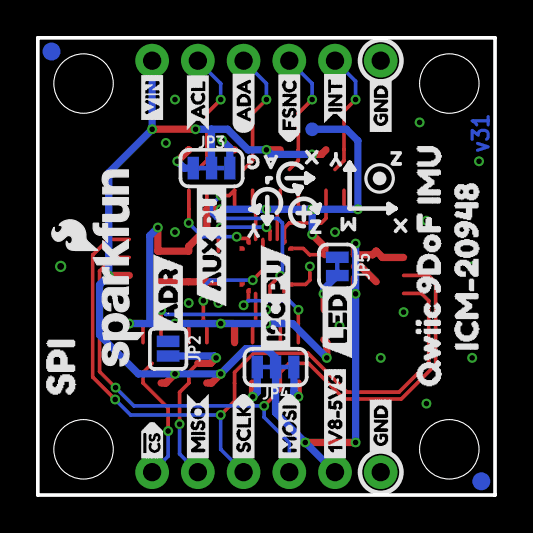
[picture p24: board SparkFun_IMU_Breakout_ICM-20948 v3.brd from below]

Board: 2 copper layers, 25.4 x 25.4 mm, 104 parts (36 on the bottom side), 26 nets.

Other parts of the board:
U$1, U$2, U$22, U$24: GND4
U$3: PWR0
U$4, U$21: INT3
U$5, U$20: FSNC2
U$6, U$19: ACL1
U$7, U$18: ADA0
U$8: MISO13
U$9: MOSI14
U$10: SCLK15
U$11: #CS16
U$12: 1V8#5V57
U$13, U$30, U$44: VIN5
U$14: NC17
U$15: CL4
U$16: DA2
U$17: AD012
U$23: ADR2
U$25: I2C_PU21
U$26: SPI19
U$27: AUX_PU24
U$28: SFE_LOGO_FLAME_.1
U$29: LED23
U$31: ICM#2094820
U$34, U$40, U$50, U$57: X0
U$35, U$41, U$51, U$58: Y1
U$36, U$42, U$52, U$59: Z2
U$37, U$60: G5
U$38, U$61: A4
U$39, U$49: M3
U$43: QWIIC_9DOF_IMU_0
U$45: I#C1

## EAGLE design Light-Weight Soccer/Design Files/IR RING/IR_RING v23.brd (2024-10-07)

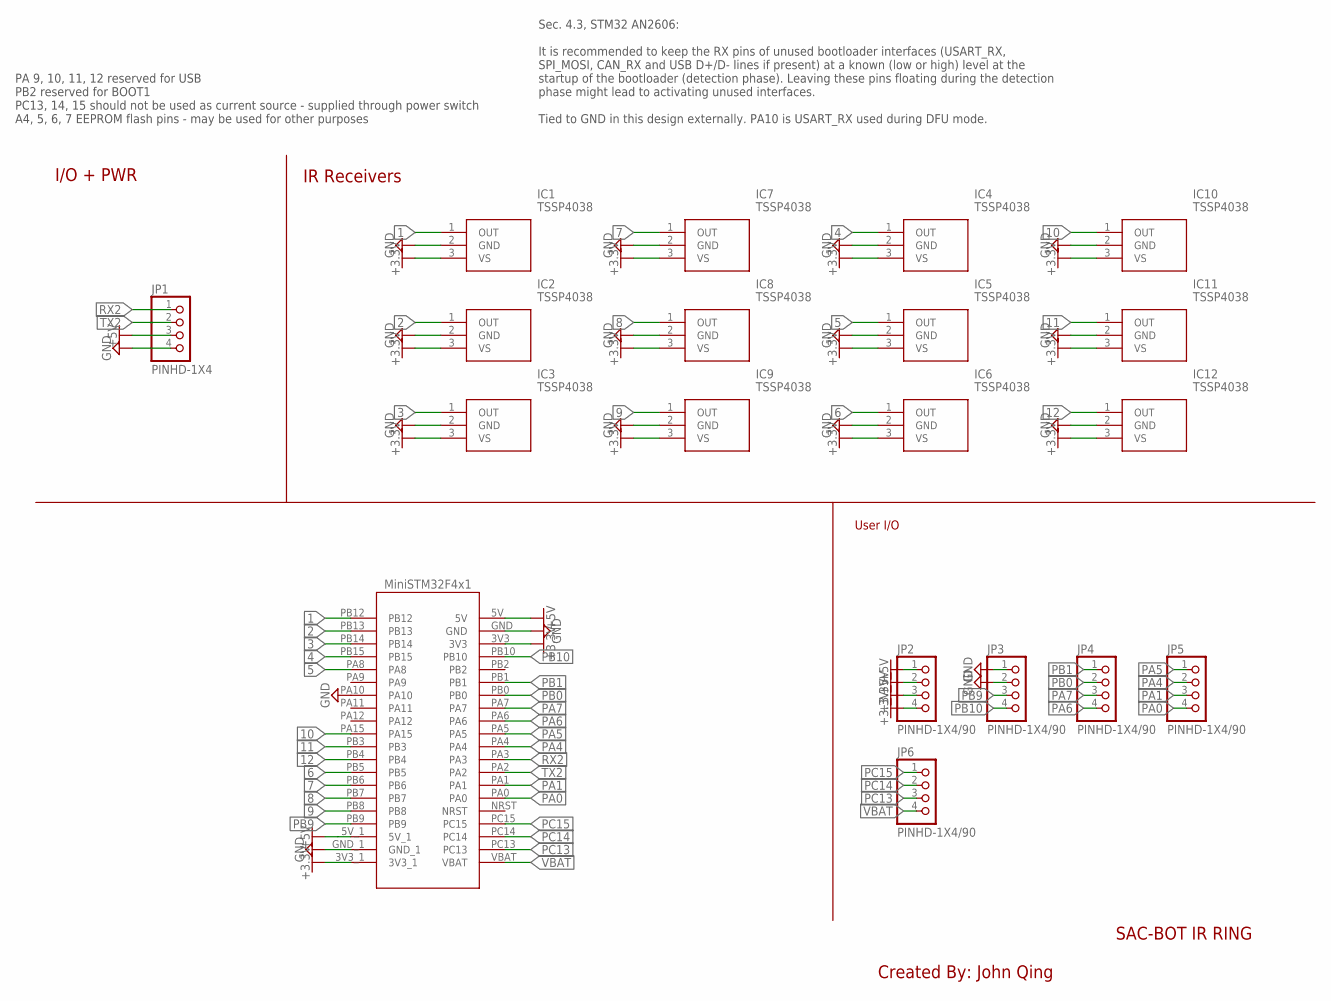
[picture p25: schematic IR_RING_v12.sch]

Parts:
IC1, IC2, IC3, IC4, IC5, IC6, IC7, IC8, IC9, IC10, IC11, IC12: TSSP4038
JP1: PINHD-1X4; 1X04
JP2, JP3, JP4, JP5, JP6: PINHD-1X4/90; 1X04/90
U$1: MINISTM32F4X1

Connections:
1: IC1.1 (OUT), U$1.PB12
2: IC2.1 (OUT), U$1.PB13
3: IC3.1 (OUT), U$1.PB14
4: IC4.1 (OUT), U$1.PB15
5: IC5.1 (OUT), U$1.PA8
6: IC6.1 (OUT), U$1.PB5
7: IC7.1 (OUT), U$1.PB6
8: IC8.1 (OUT), U$1.PB7
9: IC9.1 (OUT), U$1.PB8
10: IC10.1 (OUT), U$1.PA15
11: IC11.1 (OUT), U$1.PB3
12: IC12.1 (OUT), U$1.PB4
+3.3V: IC1.3 (VS), IC2.3 (VS), IC3.3 (VS), IC4.3 (VS), IC5.3 (VS), IC6.3 (VS), IC7.3 (VS), IC8.3 (VS), IC9.3 (VS), IC10.3 (VS), IC11.3 (VS), IC12.3 (VS), JP2.3, JP2.4, U$1.3V3, U$1.3V3_1
+5V: JP1.3, JP2.1, JP2.2, U$1.5V, U$1.5V_1
GND: IC1.2 (GND), IC2.2 (GND), IC3.2 (GND), IC4.2 (GND), IC5.2 (GND), IC6.2 (GND), IC7.2 (GND), IC8.2 (GND), IC9.2 (GND), IC10.2 (GND), IC11.2 (GND), IC12.2 (GND), JP1.4, JP3.1, JP3.2, U$1.GND, U$1.PA10
GND_1: U$1.GND_1
PA0: JP5.4, U$1.PA0
PA1: JP5.3, U$1.PA1
PA4: JP5.2, U$1.PA4
PA5: JP5.1, U$1.PA5
PA6: JP4.4, U$1.PA6
PA7: JP4.3, U$1.PA7
PB0: JP4.2, U$1.PB0
PB1: JP4.1, U$1.PB1
PB9: JP3.3, U$1.PB9
PB10: JP3.4, U$1.PB10
PC13: JP6.3, U$1.PC13
PC14: JP6.2, U$1.PC14
PC15: JP6.1, U$1.PC15
RX2: JP1.1, U$1.PA3
TX2: JP1.2, U$1.PA2
VBAT: JP6.4, U$1.VBAT

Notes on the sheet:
Created By: John Qing
SAC-BOT IR RING
IR Receivers
I/O + PWR
PA 9, 10, 11, 12 reserved for USB PB2 reserved for BOOT1 PC13, 14, 15 should not be used as current source - supplied through power switch A4, 5, 6, 7 EEPROM flash pins - may be used for other purposes
Sec. 4.3, STM32 AN2606: It is recommended to keep the RX pins of unused bootloader interfaces (USART_RX, SPI_MOSI, CAN_RX and USB D+/D- lines if present) at a known (low or high) level at the startup of the bootloader (detection phase). Leaving these pins floating during the detection phase might l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
User I/O

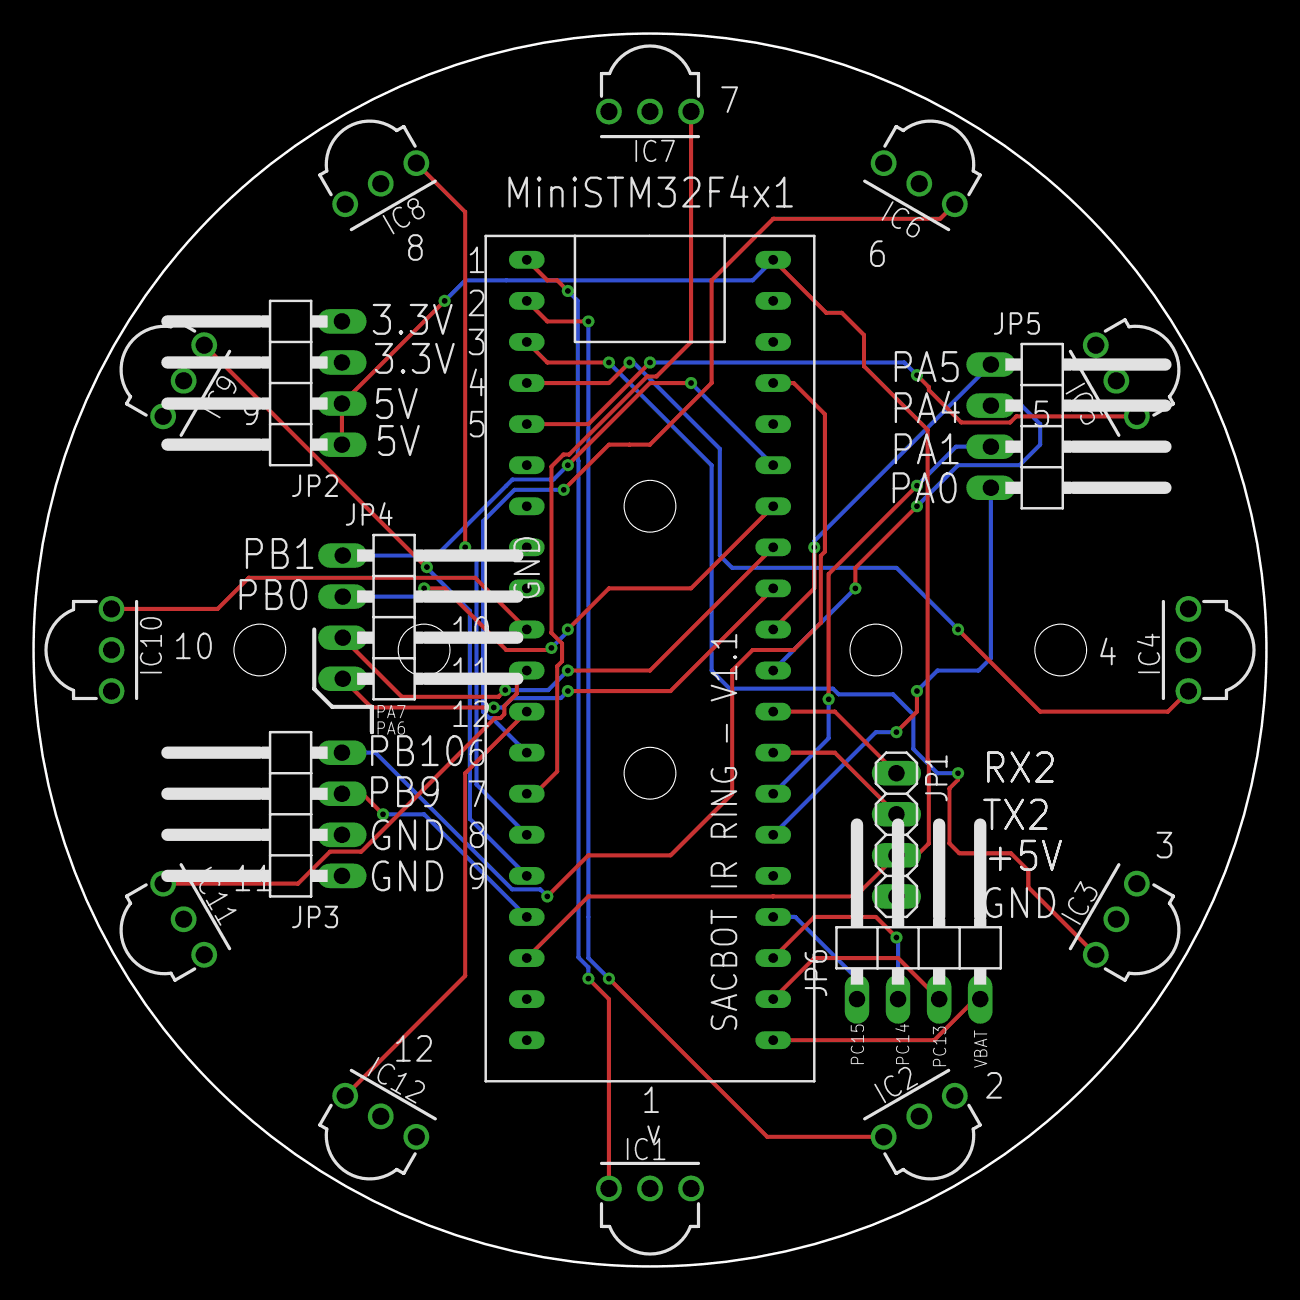
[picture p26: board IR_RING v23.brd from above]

Board: 4 copper layers, 76.2 x 76.2 mm, 19 parts (0 on the bottom side), 31 nets.

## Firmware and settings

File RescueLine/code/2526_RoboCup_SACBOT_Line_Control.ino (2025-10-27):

void setup() {
  // setting up pins for motor, ultrasonic and linefollowing sensors
  setupSensorActuator();

  // Motor test, should see:
  // left turn forwards then stop
  // right turn forward then stop
  // left turn backwards then stop
  // right turn backwards then stop
  motorControl(127,0);
  delay(300);
  motorControl(0,0);
  delay(300);
  motorControl(0,127);
  delay(300);
  motorControl(0,0);
  delay(300);
  motorControl(-127,0);
  delay(300);
  motorControl(0,0);
  delay(300);
  motorControl(0,-127);
  delay(300);
  motorControl(0,0);
  delay(300);
}

void loop() {
  // put your main code here, to run repeatedly:

  // reading distance from ultrasonic sensor
  float distance = readDistance();
 
  // reading the sensors and saving their values in _Dark variables
  int leftDark = analogRead(A2);
  int midDark = analogRead(A1);
  int rightDark = analogRead(A0);
  
  // sensor testing to serial monitor
  // printing out to Serial from sensors
  Serial.println("Distance: "+String(distance)+" leftDark: " +String(leftDark)+" midDark: "+String(midDark)+" rightDark: "+String(rightDark));
  
}


void setupSensorActuator(){
  // setting up the serial monitor and sensor pins
  Serial.begin(9600);
  // setting up sensor pins for line following
  pinMode(A0, INPUT);
  pinMode(A1, INPUT);
  pinMode(A2, INPUT);
  // setting up ultrasonic sensors as input/output
  pinMode(13, OUTPUT);
  pinMode(12, INPUT);
  // setting up motor pins as output
  pinMode(3, OUTPUT);
  pinMode(5, OUTPUT);
  pinMode(6, OUTPUT);
  pinMode(7, OUTPUT);
  pinMode(8, OUTPUT);
}
// read distance from ultrasonic sensor
float readDistance(){
  // pulse the ultrasonic speaker
  digitalWrite(13, LOW);
  delayMicroseconds(2);
  digitalWrite(13, HIGH);
  delayMicroseconds(20);
  digitalWrite(13, LOW);
  // read the time it takes to return the ultrasonic pulse
  float duration = pulseIn(12, HIGH);
  // return the distance to the main program
  return duration / 58;
}
// motor control inputs of left motor, right motor from -255 to 255
void motorControl(float leftSpeed, float rightSpeed) {
  // turning motors on
  digitalWrite(3, HIGH);
  // setting motor direction with boolean operators for HIGH/LOW ~ forward/back
  digitalWrite(8, leftSpeed > 0);
  digitalWrite(7, rightSpeed > 0);
  // finding the absolute value of motor speeds, then constraining to 0-255 and setting speed left/right
  analogWrite(6, constrain(abs(leftSpeed), 0, 255));
  analogWrite(5, constrain(abs(rightSpeed), 0, 255));
}

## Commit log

2024-07-24 fix comma issue
    [BOM.csv]
2024-09-28 final update
    [BOM.csv, BOM_complete.csv]
2024-09-28 Add design files
    [Bottom PCB v85_bom.csv, IR_RING v23_bom.csv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]
2024-09-28 Added all design files
    [Assembly_v13.f3d, Base Cover_v4.step, Bottom PCB v36.sch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]
2025-06-20 Adding v7.4 files
    [2425-SACBOT-LINE v17.f3d]
2025-10-27 fixing reversed motor/IR sensors
    [2526_RoboCup_SACBOT_Line_Control.ino]

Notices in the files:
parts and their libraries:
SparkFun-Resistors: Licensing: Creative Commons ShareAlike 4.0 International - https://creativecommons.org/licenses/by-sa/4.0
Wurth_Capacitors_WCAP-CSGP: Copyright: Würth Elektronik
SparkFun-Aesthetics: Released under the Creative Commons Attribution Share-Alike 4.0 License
